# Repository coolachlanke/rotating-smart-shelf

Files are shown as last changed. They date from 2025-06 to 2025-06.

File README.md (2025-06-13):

# Rotating Smart Shelf

Motorised display shelf for Rubik’s Cubes and other collectibles, powered by ESP32-C3 and WS2812B RGB LEDs.  
Designed for showpieces, timed rotations and eye-catching animations.

---

## 🧰 Tech Stack

- **Microcontroller:** ESP32-C3 (BLE, WiFi)
- **PCBs:** Custom power distrubution/driver/logic board + annular 48-pixel WS21812B carrier board. All designed in KiCAD 8.
- **Motors:** NEMA17 bipolar stepper motors with A4988 drivers
- **Power:** 9V barrel input with onboard 5V & 3V3 voltage regulation
- **Firmware:** Custom C++ firmware utiliting FreeRTOS built with PlatformIO (Arduino framework)
- **Lighting:** WS2812B addressable RGB LED rings for reactive effects
- **Control App:** Web-app interface for wireless control and presets
- **Features:**
  - Smooth timed rotation of platforms
  - Colour animations, brightness modulation, visual syncing
  - [UNDER CONSTRUCTION] Optional music-reactive visuals (via onboard mic or wireless data stream)

---

> Designed by Lachlan Cooke in late 2024.
> Check out [lachlancooke.com/projects](https://www.lachlancooke.com/projects) für mehr details.

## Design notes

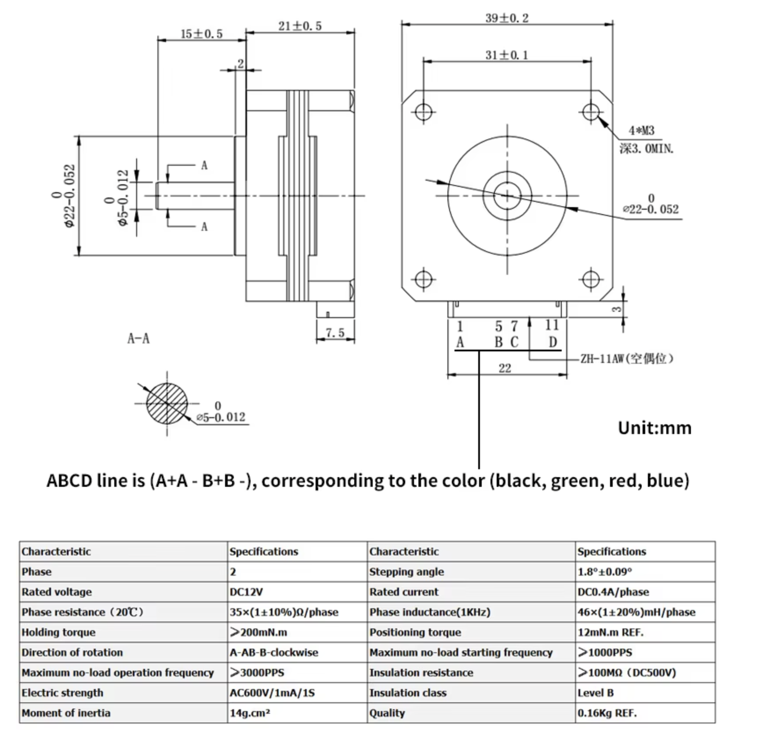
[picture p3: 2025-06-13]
Images/17HS08-1004S_Schematic.png

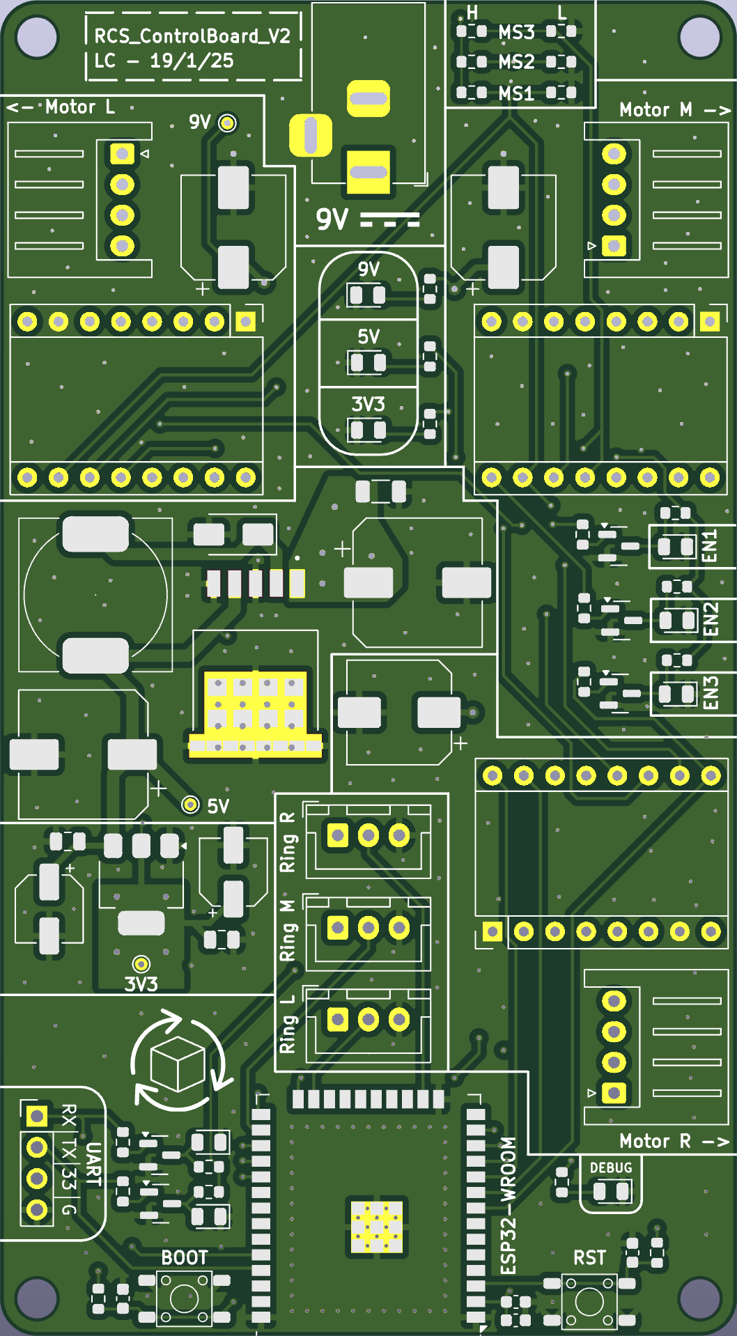
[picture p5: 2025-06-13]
CAD/Mechanical/3DP_Outjobs/RCS_Proto_V2/RCS_Logic_V2_FrontSilk.png

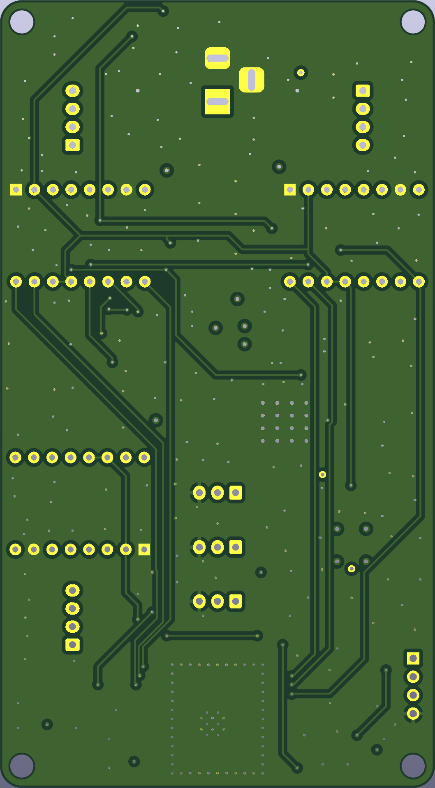
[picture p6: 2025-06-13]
CAD/Mechanical/3DP_Outjobs/RCS_Proto_V2/RCS_Logic_V2_BottomSilk.png

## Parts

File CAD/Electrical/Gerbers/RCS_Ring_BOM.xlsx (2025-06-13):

Comment | Designator | Footprint | JLCPCB Part #
100nF | C1, C2, C3, C4, C5, C6, C7, C8, C9, C10, C11, C12, C13, C14, C15, C16, C17, C18, C19, C20, C21, C22, C23, C24, C25, C26, C27, C28, C29, C30, C31, C32, C33, C34, C35, C36, C37, C38, C39, C40, C41, C42, C43, C44, C45, C46, C47, C48 | C0603 | C14663
WS2812B | D1, D2, D3, D4, D5, D6, D7, D8, D9, D10, D11, D12, D13, D14, D15, D16, D17, D18, D19, D20, D21, D22, D23, D24, D25, D26, D27, D28, D29, D30, D31, D32, D33, D34, D35, D36, D37, D38, D39, D40, D41, D42, D43, D44, D45, D46, D47, D48 | LED_WS2812B-2020_PLCC4_2.0x2.0mm | C965555

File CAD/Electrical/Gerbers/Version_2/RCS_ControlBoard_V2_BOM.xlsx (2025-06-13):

Comment | Designator | Footprint | JLCPCB Part #
100u Electrolytic | C1,C5,C9 | Capacitor_SMD:CP_Elec_8x10 | C116241
680u Electrolytic | C2 | Capacitor_SMD:CP_Elec_10x10 | C340751
1u 1206 | C3 | Capacitor_SMD:C_1206_3216Metric | C1848
220u Electrolytic | C4 | Capacitor_SMD:CP_Elec_10x10 | C125977
10u Electrolytic | C6,C8 | Capacitor_SMD:CP_Elec_5x5.4 | C4747971
10u 0603 | C14 | Capacitor_SMD:C_0603_1608Metric | C19702
0.1u 0805 | C7,C12 | Capacitor_SMD:C_0805_2012Metric | C28233
0.1u 0603 | C10,C11,C13 | Capacitor_SMD:C_0603_1608Metric | C1588
SS34 | D1 | Diode_SMD:D_SMA | C8678
LED (GRE) | D2,D3,D4 | Diode_SMD:D_0805_2012Metric | C965815
LED (RED) | D5,D8,D9 | Diode_SMD:D_0805_2012Metric | C965812
LED (BLU) | D6, D10 | Diode_SMD:D_0805_2012Metric | C965817
LED (YEL) | D7 | Diode_SMD:D_0805_2012Metric | C965814
Barrel_Jack | J1 | Connector_BarrelJack:BarrelJack_Horizontal | C136744
Conn_01x04 | J2,J3,J4 | Connector_JST:JST_XH_S4B-XH-A_1x04_P2.50mm_Horizontal | C157925
Conn_01x03 | J5,J6,J7 | Connector_JST:JST_XH_B3B-XH-A_1x03_P2.50mm_Vertical | C161870
Conn_01x04_Pin | J8 | Connector_PinHeader_2.54mm:PinHeader_1x04_P2.54mm_Vertical | C2691448
33uH | L1 | LC_CustomFootprint:SMDRI127 | C9400
BC817 | Q1,Q2,Q3,Q4,Q5 | Package_TO_SOT_SMD:SOT-23 | C52801
0R | R1,R2,R3,R19,R20,R21 | Resistor_SMD:R_0603_1608Metric | C21189
750R | R4, R22 | Resistor_SMD:R_0603_1608Metric | C23179
1k | R7,R8,R9,R10,R15,R16,R17,R18 | Resistor_SMD:R_0603_1608Metric | C21190
2k4 | R5 | Resistor_SMD:R_0603_1608Metric | C22940
6k2 | R6 | Resistor_SMD:R_0603_1608Metric | C4260
10k | R11,R12,R13,R14 | Resistor_SMD:R_0603_1608Metric | C25804
SW_Push | SW1,SW2 | LC_CustomFootprint:SW_PUSH_4.5mm | C455243
LM2596S-5 | U1 | Package_TO_SOT_SMD:TO-263-5_TabPin3 | C10002
AMS1117-3.3 | U3 | Package_TO_SOT_SMD:SOT-223-3_TabPin2 | C6186
ESP32-WROOM-32-N4 | U2 | RF_Module:ESP32-WROOM-32 | C82899

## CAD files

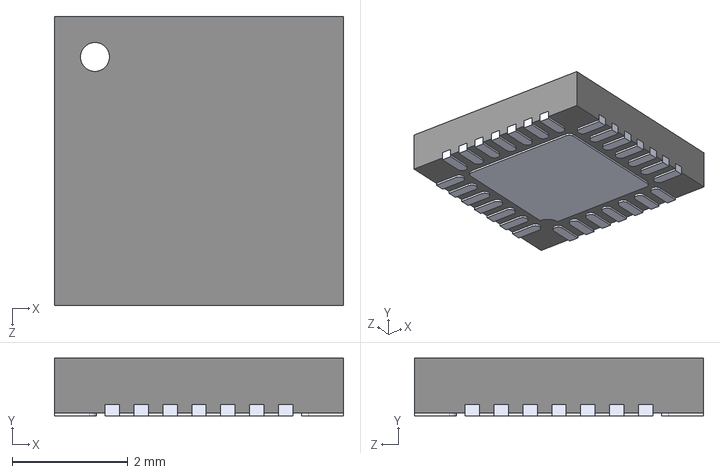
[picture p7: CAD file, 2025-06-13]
CAD/Electrical/Components/A4988SETTR_T/A4988SETTR-T.step
5.00 x 1.00 x 5.00 mm

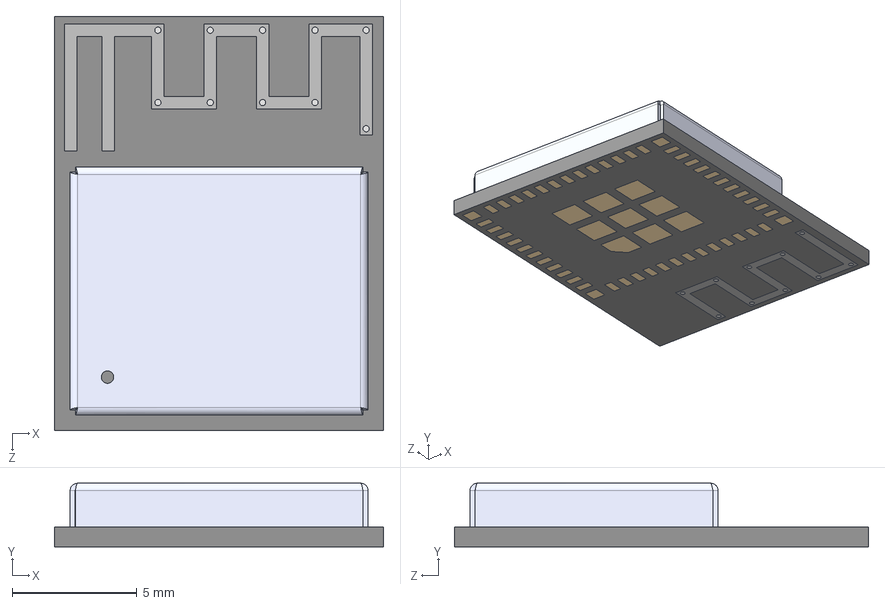
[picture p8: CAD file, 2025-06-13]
CAD/Electrical/Components/ESP32_C3_MINI_1_N4/ESP32-C3-MINI-1-N4.step
13.2 x 2.55 x 16.6 mm

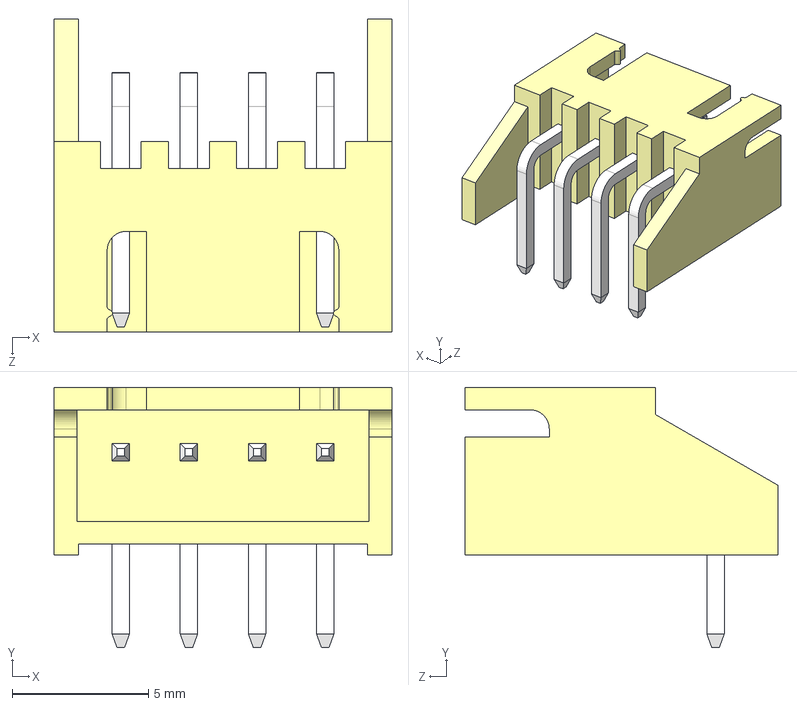
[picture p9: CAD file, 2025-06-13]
CAD/Electrical/Components/S4B-XH-A_LF__SN_/S4B-XH-A_LF__SN_.step
12.4 x 9.55 x 11.5 mm

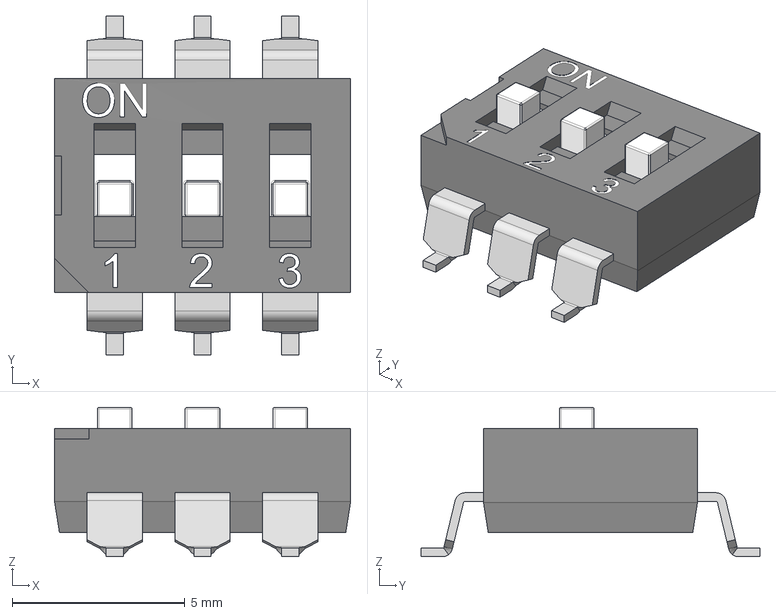
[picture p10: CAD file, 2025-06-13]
CAD/Electrical/Components/SMD DIP SWITCH 3P.step
8.56 x 9.80 x 4.32 mm

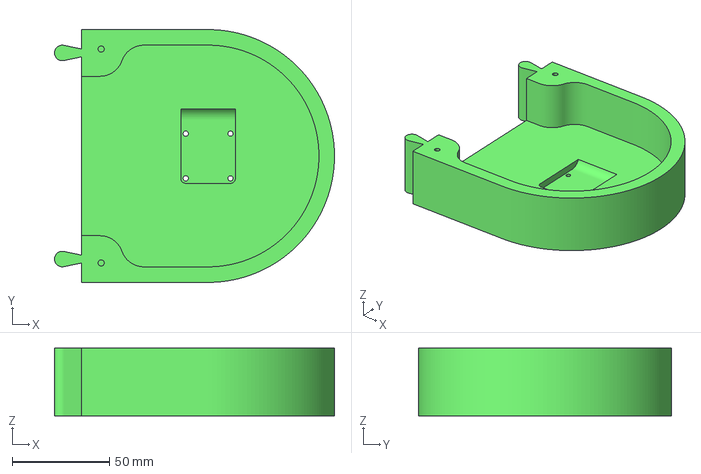
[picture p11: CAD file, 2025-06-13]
CAD/Mechanical/3DP_Outjobs/Alternate_RCS/ARCS_FrameLower_R.3mf
144.0 x 130.0 x 34.8 mm

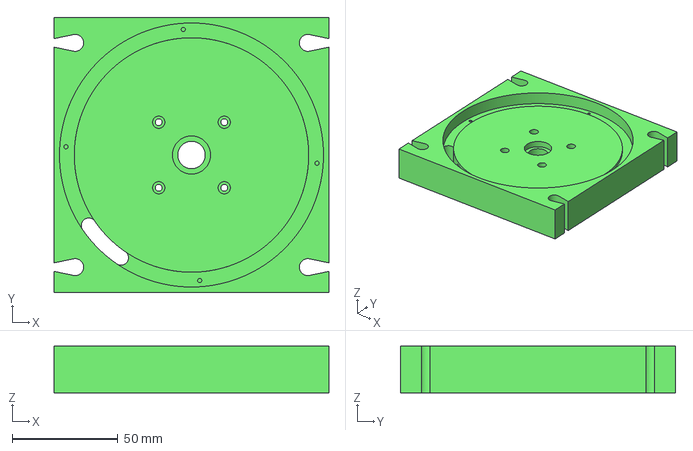
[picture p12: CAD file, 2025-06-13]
CAD/Mechanical/3DP_Outjobs/RCS_Proto_V2/Frame_M_Long.3mf
130.0 x 130.0 x 22.0 mm

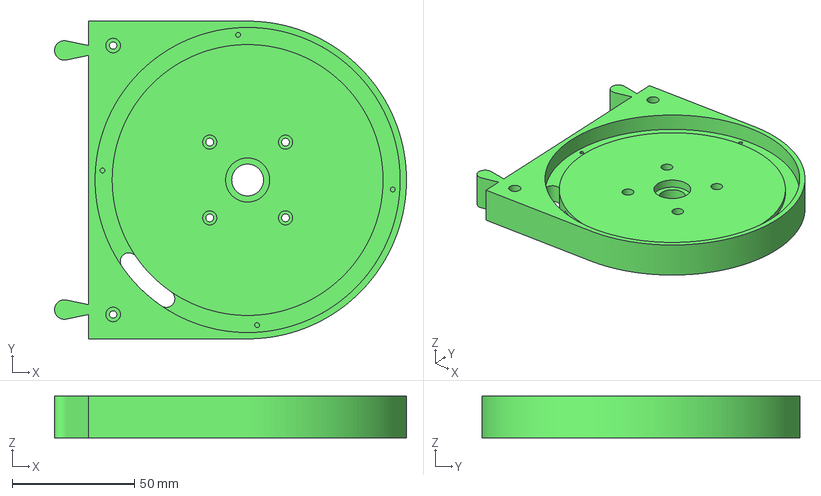
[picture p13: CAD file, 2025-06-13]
CAD/Mechanical/Current Models/2RCS_Frame_R.3mf
144.0 x 130.0 x 17.0 mm

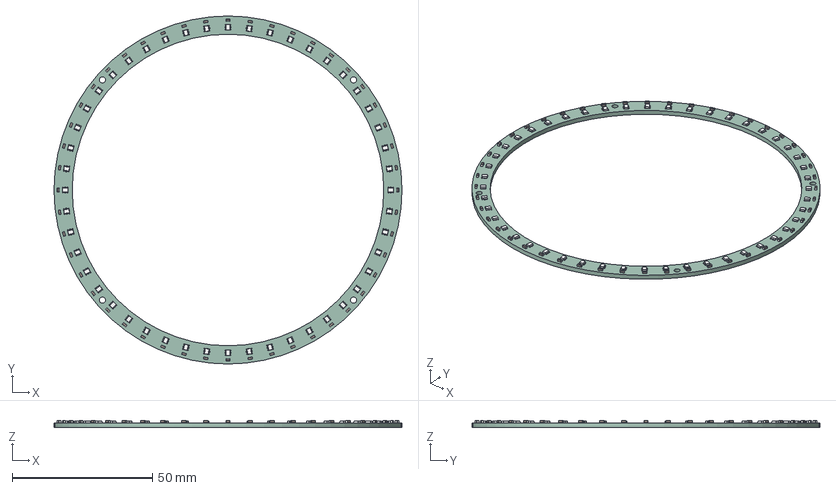
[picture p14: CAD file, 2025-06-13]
CAD/Mechanical/KiCAD_Models/RCS_WS2812B_Ring.step
124.0 x 124.0 x 2.45 mm
WS2812-2020 x 48
C_0603_1608Metric x 48
RCS_WS2812B_Ring_PCB

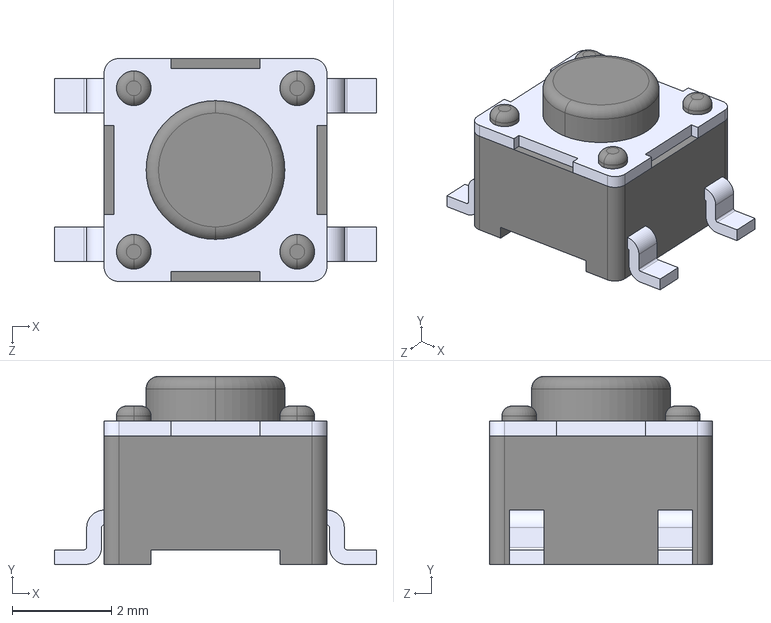
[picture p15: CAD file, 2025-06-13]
CAD/Electrical/Components/PTS 647 SM38 SMTR2 LFS--3DModel-STEP-269445.STEP
6.50 x 3.80 x 4.50 mm

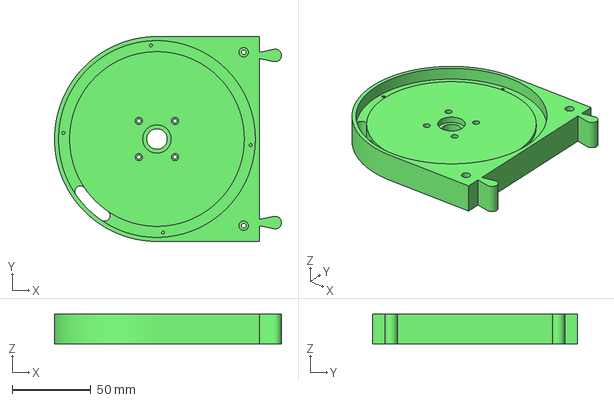
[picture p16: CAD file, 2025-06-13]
CAD/Mechanical/3DP_Outjobs/Alternate_RCS/ARCS_Frame_L2.3mf
144.0 x 130.0 x 19.0 mm

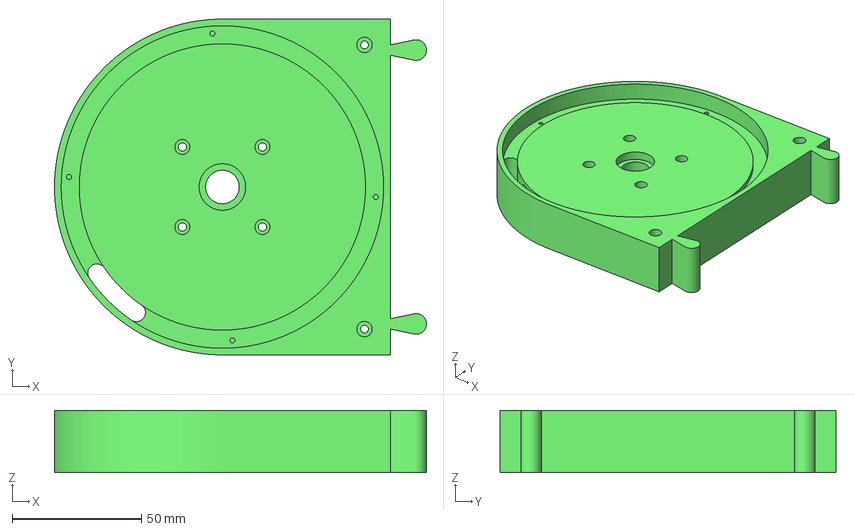
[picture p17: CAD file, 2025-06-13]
CAD/Mechanical/3DP_Outjobs/RCS_Proto_V2/Frame_L_Max.3mf
144.0 x 130.0 x 24.0 mm

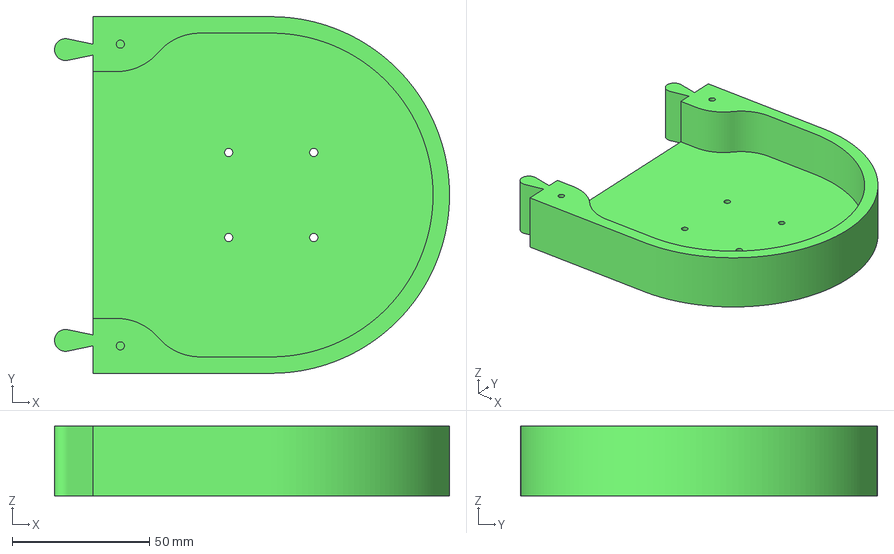
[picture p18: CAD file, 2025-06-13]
CAD/Mechanical/Current Models/2RCS_FrameLower_R.3mf
144.0 x 130.0 x 25.5 mm

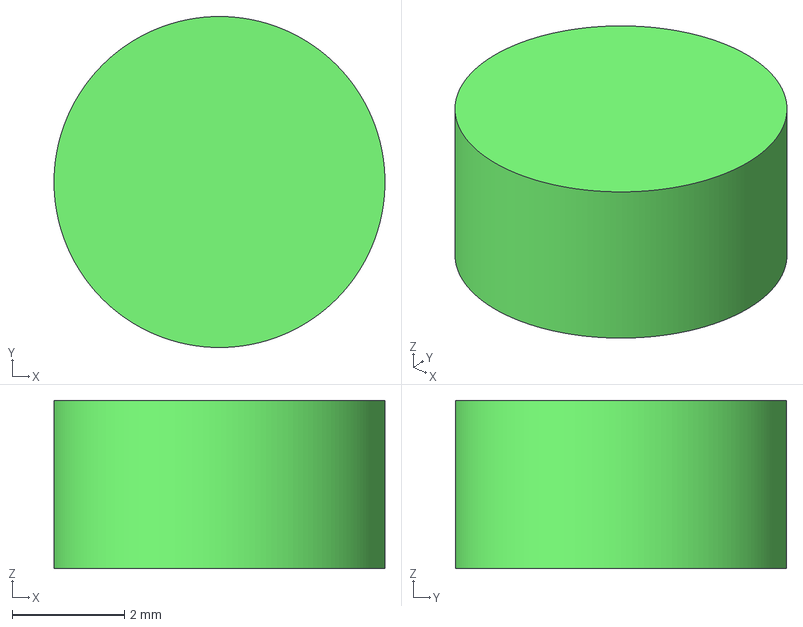
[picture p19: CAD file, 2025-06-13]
CAD/Mechanical/3DP_Outjobs/Alternate_RCS/ARCS_Cap2.3mf
5.90 x 5.90 x 3.00 mm

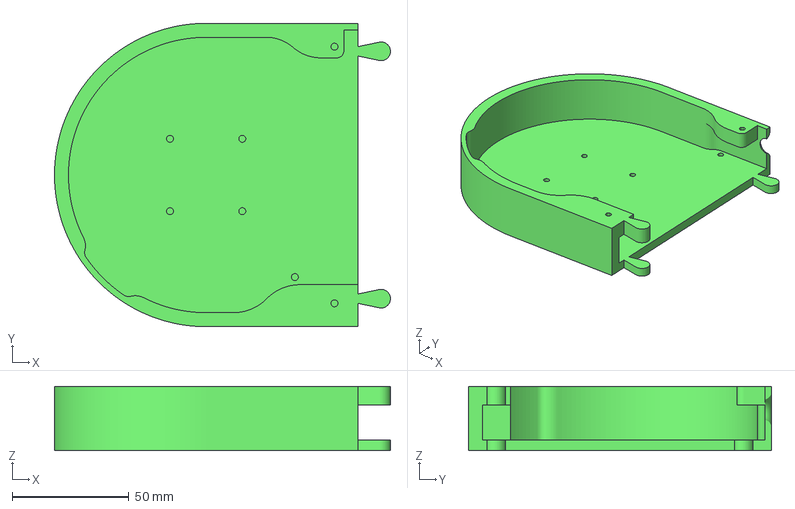
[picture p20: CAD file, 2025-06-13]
CAD/Mechanical/3DP_Outjobs/RCS_Proto_V2/FrameLower_L_MAX.3mf
144.0 x 130.0 x 27.5 mm

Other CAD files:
CAD/Mechanical/Current Models/2RCS_FrameLower_M.3mf
CAD/Electrical/Components/L_12x12mm_H8mm.step
CAD/Mechanical/3DP_Outjobs/Alternate_RCS/ARCS_Frame_L.3mf
CAD/Mechanical/3DP_Outjobs/Alternate_RCS/ARCS_Cap.3mf
CAD/Mechanical/3DP_Outjobs/Alternate_RCS/ARCS_FrameLower_L.3mf
CAD/Mechanical/3DP_Outjobs/Alternate_RCS/ARCS_FrameLower_L2.3mf
CAD/Mechanical/3DP_Outjobs/Alternate_RCS/ARCS_FrameLower_M.3mf
CAD/Mechanical/3DP_Outjobs/Alternate_RCS/ARCS_FrameLower_M_ALT.3mf
CAD/Mechanical/3DP_Outjobs/Alternate_RCS/ARCS_FrameLower_R2.3mf
CAD/Mechanical/3DP_Outjobs/Alternate_RCS/ARCS_Frame_M.3mf
CAD/Mechanical/3DP_Outjobs/Alternate_RCS/ARCS_Frame_R.3mf
CAD/Mechanical/3DP_Outjobs/Alternate_RCS/ARCS_Frame_R2.3mf
CAD/Mechanical/3DP_Outjobs/Alternate_RCS/ARCS_Platform.3mf
CAD/Mechanical/3DP_Outjobs/Alternate_RCS/ARCS_Platform2.3mf
CAD/Mechanical/3DP_Outjobs/RCS_Proto_V1/Diffuser.3mf
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

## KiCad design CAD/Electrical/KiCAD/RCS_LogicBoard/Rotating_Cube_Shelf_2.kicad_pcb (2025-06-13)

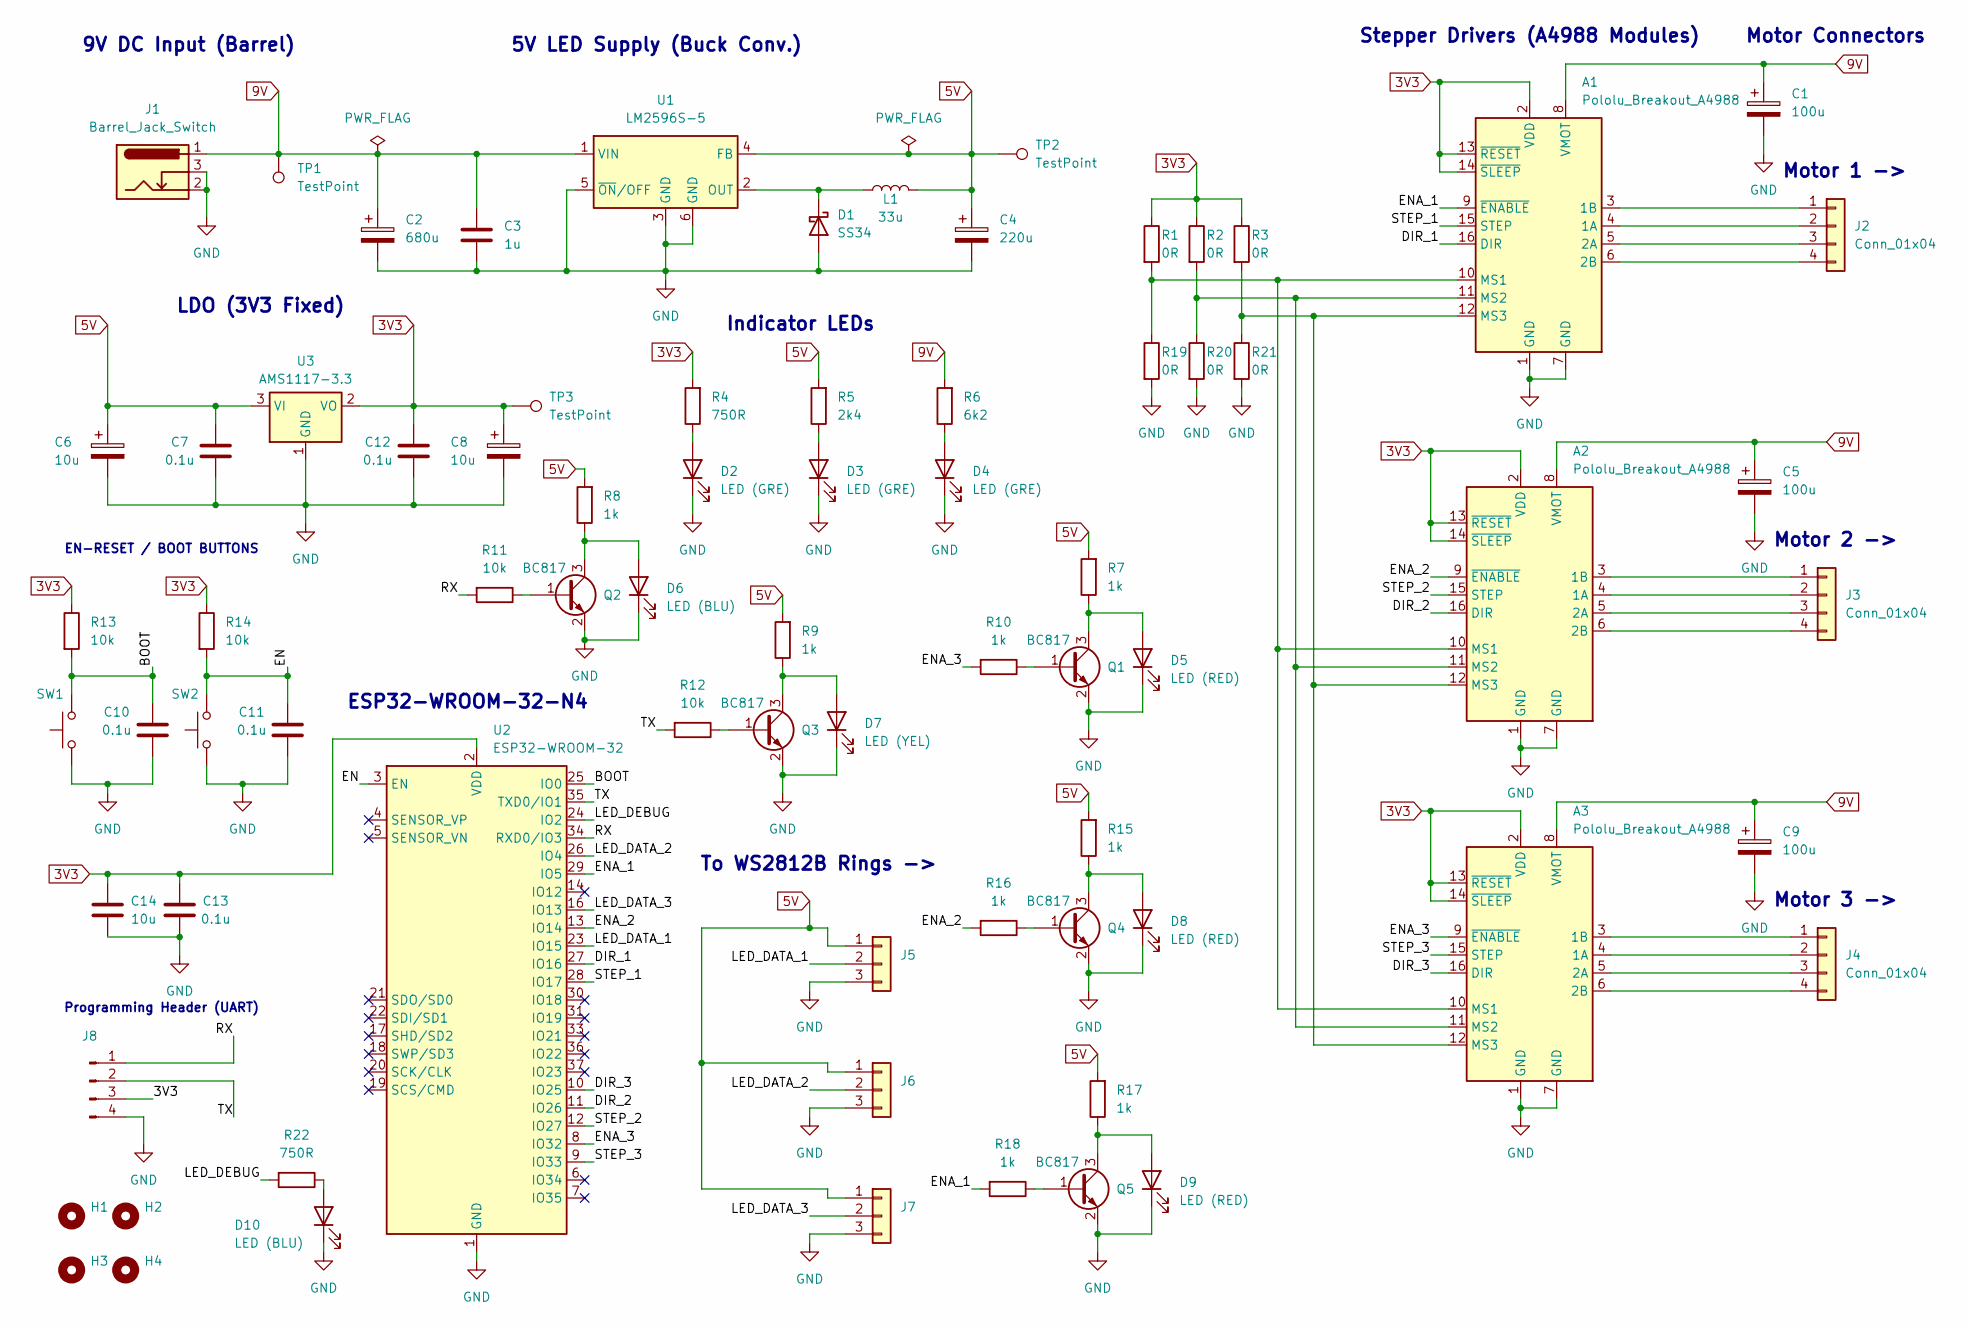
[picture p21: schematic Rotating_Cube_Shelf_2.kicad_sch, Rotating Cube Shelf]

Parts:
A1, A2, A3: Pololu_Breakout_A4988; Pololu_Breakout-16_15.2x20.3mm
C1, C5, C9: 100u; CP_Elec_8x10; LCSC C116241
C2: 680u; CP_Elec_10x10; LCSC C340751
C3: 1u; C_1206_3216Metric
C4: 220u; CP_Elec_10x10; LCSC C125977
C6, C8: 10u; CP_Elec_5x5.4; LCSC C4747971
C7, C12: 0.1u; C_0805_2012Metric
C10, C11, C13: 0.1u; C_0603_1608Metric
C14: 10u; C_0603_1608Metric
D1: SS34; D_SMA
D2, D3, D4: LED (GRE); D_0805_2012Metric; LCSC C965815
D5, D8, D9: LED (RED); D_0805_2012Metric; LCSC C965812
D6, D10: LED (BLU); D_0805_2012Metric; LCSC C965817
D7: LED (YEL); D_0805_2012Metric; LCSC C965814
H1, H2, H3, H4: MountingHole; MountingHole_3.2mm_M3
J1: Barrel_Jack_Switch; BarrelJack_Horizontal; LCSC C136744
J2, J3, J4: Conn_01x04; JST_XH_S4B-XH-A_1x04_P2.50mm_Horizontal; LCSC C157925
J5, J6, J7: Conn_01x03; JST_XH_B3B-XH-A_1x03_P2.50mm_Vertical; LCSC C161870
J8: Conn_01x04_Pin; PinHeader_1x04_P2.54mm_Vertical; LCSC C2691448
L1: 33u; SMDRI127; LCSC C9400
Q1, Q2, Q3, Q4, Q5: BC817; SOT-23; LCSC C52801
R1, R2, R3, R19, R20, R21: 0R; R_0603_1608Metric
R4, R22: 750R; R_0603_1608Metric
R5: 2k4; R_0603_1608Metric
R6: 6k2; R_0603_1608Metric
R7, R8, R9, R10, R15, R16, R17, R18: 1k; R_0603_1608Metric
R11, R12, R13, R14: 10k; R_0603_1608Metric
SW1, SW2: SW_Push; SW_PUSH_4.5mm; LCSC C455243
TP1, TP2, TP3: TestPoint; TestPoint_THTPad_D1.0mm_Drill0.5mm
U1: LM2596S-5; VREG_LM2596SX-5.0_NOPB
U2: ESP32-WROOM-32; LCSC C82899
U3: AMS1117-3.3; SOT-223-3_TabPin2; LCSC C6186

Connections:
3V3: A1.2 (VDD), A1.13 (~RESET), A1.14 (~SLEEP), A2.2 (VDD), A2.13 (~RESET), A2.14 (~SLEEP), A3.2 (VDD), A3.13 (~RESET), A3.14 (~SLEEP), C8.1, C12.2, C13.2, C14.2, J8.3, R1.1, R2.1, R3.1, R4.2, R13.1, R14.1, TP3.1, U2.2 (VDD), U3.2 (VO)
5V: C4.1, C6.1, C7.2, J5.1, J6.1, J7.1, L1.2, R5.2, R7.2, R8.2, R9.2, R15.2, R17.2, TP2.1, U1.4 (FB), U3.3 (VI)
9V: A1.8 (VMOT), A2.8 (VMOT), A3.8 (VMOT), C1.1, C2.1, C3.2, C5.1, C9.1, J1.1, R6.2, TP1.1, U1.1 (VIN)
/BOOT: C10.2, R13.2, SW1.2, U2.25 (IO0)
/DIR_1: A1.16 (DIR), U2.27 (IO16)
/DIR_2: A2.16 (DIR), U2.11 (IO26)
/DIR_3: A3.16 (DIR), U2.10 (IO25)
/EN: C11.2, R14.2, SW2.2, U2.3 (EN)
/ENA_1: A1.9 (~ENABLE), R18.2, U2.29 (IO5)
/ENA_2: A2.9 (~ENABLE), R16.2, U2.13 (IO14)
/ENA_3: A3.9 (~ENABLE), R10.2, U2.8 (IO32)
/LED_DATA_1: J5.2, U2.23 (IO15)
/LED_DATA_2: J6.2, U2.26 (IO4)
/LED_DATA_3: J7.2, U2.16 (IO13)
/LED_DEBUG: R22.2, U2.24 (IO2)
/RX: J8.1, R11.2, U2.34 (RXD0/IO3)
/STEP_1: A1.15 (STEP), U2.28 (IO17)
/STEP_2: A2.15 (STEP), U2.12 (IO27)
/STEP_3: A3.15 (STEP), U2.9 (IO33)
/TX: J8.2, R12.2, U2.35 (TXD0/IO1)
GND: A1.1 (GND), A1.7 (GND), A2.1 (GND), A2.7 (GND), A3.1 (GND), A3.7 (GND), C1.2, C2.2, C3.1, C4.2, C5.2, C6.2, C7.1, C8.2, C9.2, C10.1, C11.1, C12.1, C13.1, C14.1, D1.2 (A), D2.1 (K), D3.1 (K), D4.1 (K), D5.1 (K), D6.1 (K), D7.1 (K), D8.1 (K), D9.1 (K), D10.1 (K), J1.2, J1.3, J5.3, J6.3, J7.3, J8.4, Q1.2 (E), Q2.2 (E), Q3.2 (E), Q4.2 (E), Q5.2 (E), R19.2, R20.2, R21.2, SW1.1, SW2.1, U1.3 (GND), U1.5 (~ON/OFF), U1.6 (GND), U2.1 (GND), U2.15 (GND), U2.38 (GND), U2.39 (GND), U3.1 (GND)
unnamed: A1.4 (1A), J2.2
unnamed: A1.3 (1B), J2.1
unnamed: A1.5 (2A), J2.3
unnamed: A1.6 (2B), J2.4
unnamed: A1.10 (MS1), A2.10 (MS1), A3.10 (MS1), R1.2, R19.1
unnamed: A1.11 (MS2), A2.11 (MS2), A3.11 (MS2), R2.2, R20.1
unnamed: A1.12 (MS3), A2.12 (MS3), A3.12 (MS3), R3.2, R21.1
unnamed: A2.4 (1A), J3.2
unnamed: A2.3 (1B), J3.1
unnamed: A2.5 (2A), J3.3
unnamed: A2.6 (2B), J3.4
unnamed: A3.4 (1A), J4.2
unnamed: A3.3 (1B), J4.1
unnamed: A3.5 (2A), J4.3
unnamed: A3.6 (2B), J4.4
unnamed: D1.1 (K), L1.1, U1.2 (OUT)
unnamed: D2.2 (A), R4.1
unnamed: D3.2 (A), R5.1
unnamed: D4.2 (A), R6.1
unnamed: D5.2 (A), Q1.3 (C), R7.1
unnamed: D6.2 (A), Q2.3 (C), R8.1
unnamed: D7.2 (A), Q3.3 (C), R9.1
unnamed: D8.2 (A), Q4.3 (C), R15.1
unnamed: D9.2 (A), Q5.3 (C), R17.1
unnamed: D10.2 (A), R22.1
unnamed: Q1.1 (B), R10.1
unnamed: Q2.1 (B), R11.1
unnamed: Q3.1 (B), R12.1
unnamed: Q4.1 (B), R16.1
unnamed: Q5.1 (B), R18.1

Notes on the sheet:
Stepper Drivers (A4988 Modules)
5V LED Supply (Buck Conv.)
EN-RESET / BOOT BUTTONS
To WS2812B Rings ->
Motor 3 ->
9V DC Input (Barrel)
Motor Connectors
Programming Header (UART)
Indicator LEDs
ESP32-WROOM-32-N4
Motor 1 ->
LDO (3V3 Fixed)
Motor 2 ->

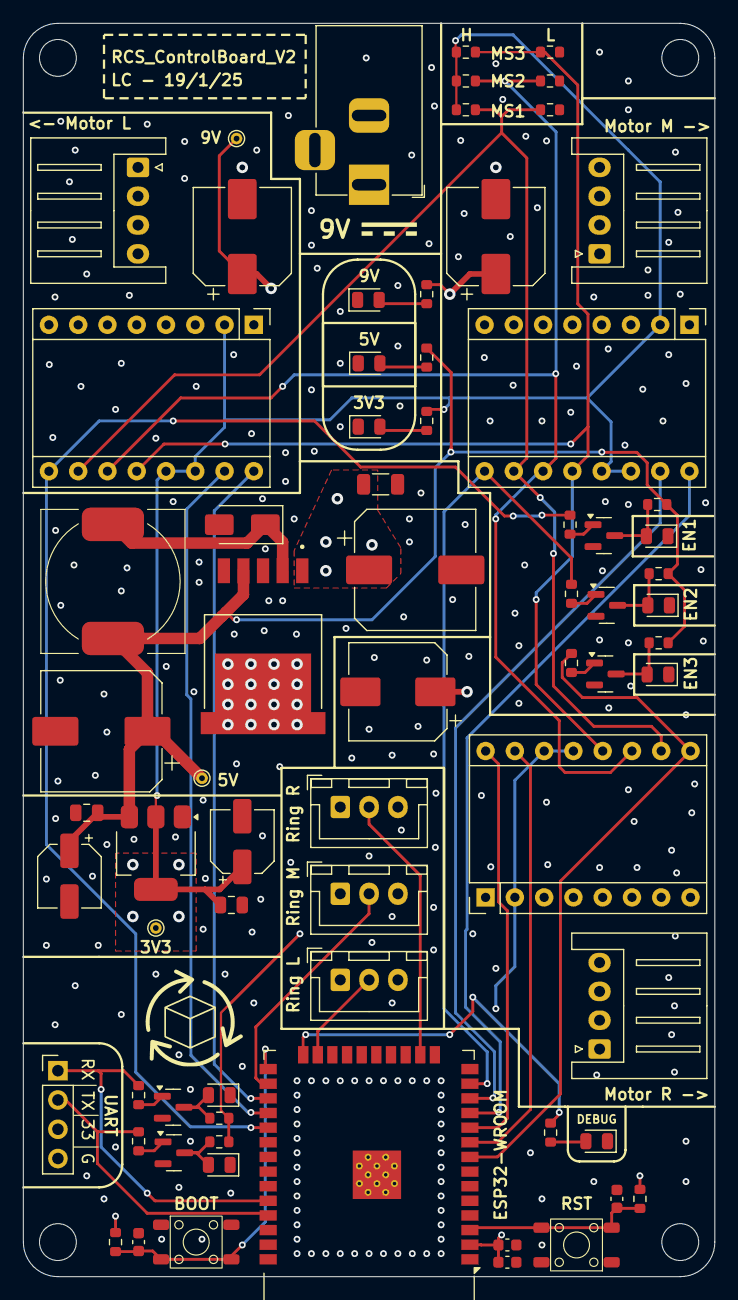
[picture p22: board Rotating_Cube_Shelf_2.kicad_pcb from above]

Board: 4 copper layers, 60.0 x 108.8 mm, 75 parts (0 on the bottom side), 51 nets.

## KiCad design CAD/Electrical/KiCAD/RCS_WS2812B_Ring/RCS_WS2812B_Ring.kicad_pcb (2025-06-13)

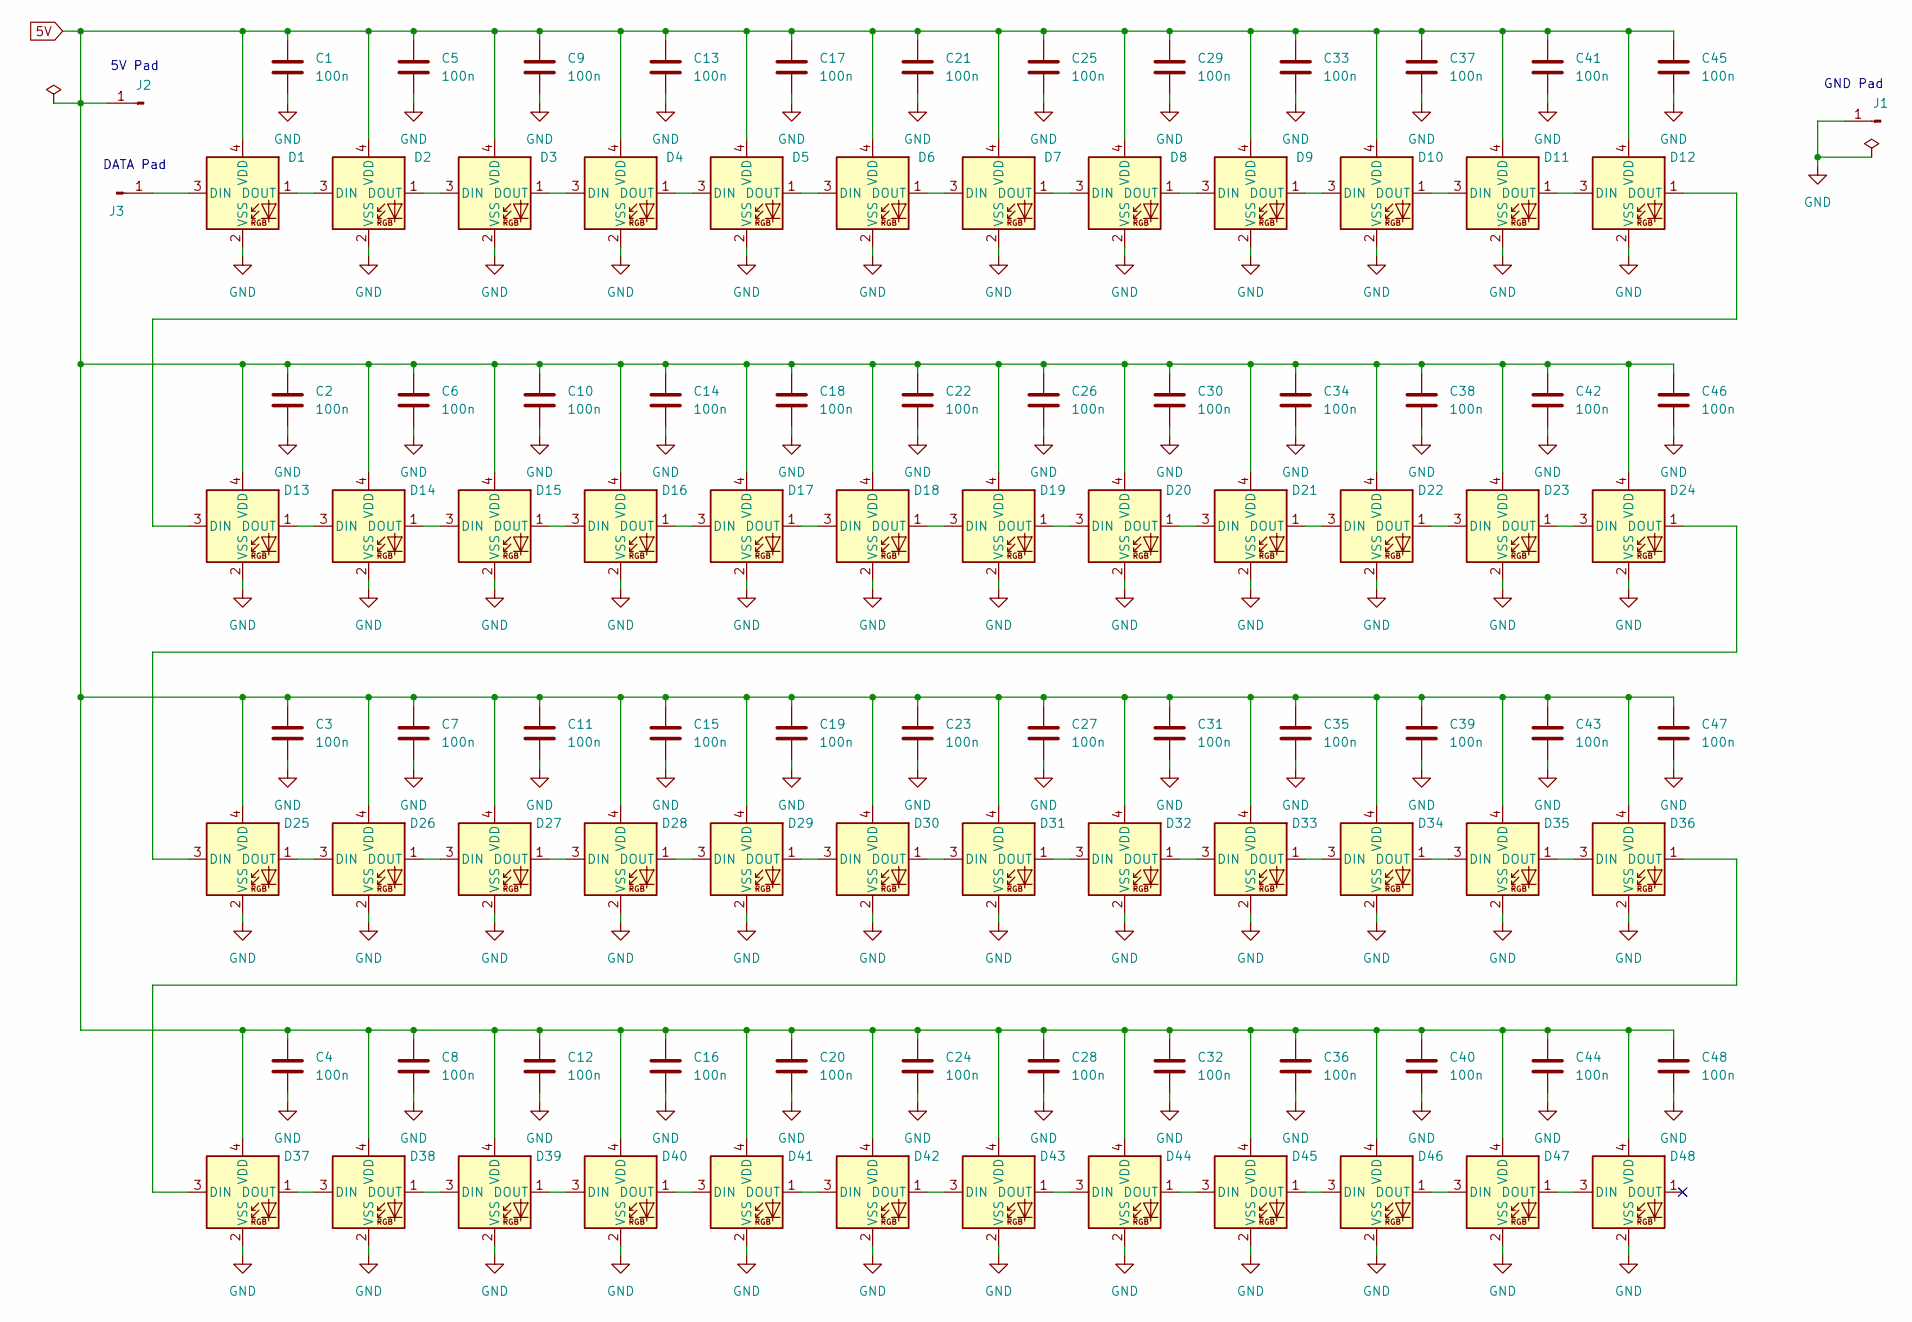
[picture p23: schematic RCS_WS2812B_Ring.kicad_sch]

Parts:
C1, C2, C3, C4, C5, C6, C7, C8, C9, C10, C11, C12, C13, C14, C15, C16, C17, C18, C19, C20, C21, C22, C23, C24, C25, C26, C27, C28, C29, C30, C31, C32, C33, C34, C35, C36, C37, C38, C39, C40, C41, C42, C43, C44, C45, C46, C47, C48: 100n; C_0603_1608Metric
D1, D2, D3, D4, D5, D6, D7, D8, D9, D10, D11, D12, D13, D14, D15, D16, D17, D18, D19, D20, D21, D22, D23, D24, D25, D26, D27, D28, D29, D30, D31, D32, D33, D34, D35, D36, D37, D38, D39, D40, D41, D42, D43, D44, D45, D46, D47, D48: WS2812B-2020; LED_WS2812B-2020_PLCC4_2.0x2.0mm
J1, J2, J3: Conn_01x01_Pin; PAD_WS2812B_RING

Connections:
5V: C1.1, C2.1, C3.1, C4.1, C5.1, C6.1, C7.1, C8.1, C9.1, C10.1, C11.1, C12.1, C13.1, C14.1, C15.1, C16.1, C17.1, C18.1, C19.1, C20.1, C21.1, C22.1, C23.1, C24.1, C25.1, C26.1, C27.1, C28.1, C29.1, C30.1, C31.1, C32.1, C33.1, C34.1, C35.1, C36.1, C37.1, C38.1, C39.1, C40.1, C41.1, C42.1, C43.1, C44.1, C45.1, C46.1, C47.1, C48.1, D1.4 (VDD), D2.4 (VDD), D3.4 (VDD), D4.4 (VDD), D5.4 (VDD), D6.4 (VDD), D7.4 (VDD), D8.4 (VDD), D9.4 (VDD), D10.4 (VDD), D11.4 (VDD), D12.4 (VDD), D13.4 (VDD), D14.4 (VDD), D15.4 (VDD), D16.4 (VDD), D17.4 (VDD), D18.4 (VDD), D19.4 (VDD), D20.4 (VDD), D21.4 (VDD), D22.4 (VDD), D23.4 (VDD), D24.4 (VDD), D25.4 (VDD), D26.4 (VDD), D27.4 (VDD), D28.4 (VDD), D29.4 (VDD), D30.4 (VDD), D31.4 (VDD), D32.4 (VDD), D33.4 (VDD), D34.4 (VDD), D35.4 (VDD), D36.4 (VDD), D37.4 (VDD), D38.4 (VDD), D39.4 (VDD), D40.4 (VDD), D41.4 (VDD), D42.4 (VDD), D43.4 (VDD), D44.4 (VDD), D45.4 (VDD), D46.4 (VDD), D47.4 (VDD), D48.4 (VDD), J2.1
GND: C1.2, C2.2, C3.2, C4.2, C5.2, C6.2, C7.2, C8.2, C9.2, C10.2, C11.2, C12.2, C13.2, C14.2, C15.2, C16.2, C17.2, C18.2, C19.2, C20.2, C21.2, C22.2, C23.2, C24.2, C25.2, C26.2, C27.2, C28.2, C29.2, C30.2, C31.2, C32.2, C33.2, C34.2, C35.2, C36.2, C37.2, C38.2, C39.2, C40.2, C41.2, C42.2, C43.2, C44.2, C45.2, C46.2, C47.2, C48.2, D1.2 (VSS), D2.2 (VSS), D3.2 (VSS), D4.2 (VSS), D5.2 (VSS), D6.2 (VSS), D7.2 (VSS), D8.2 (VSS), D9.2 (VSS), D10.2 (VSS), D11.2 (VSS), D12.2 (VSS), D13.2 (VSS), D14.2 (VSS), D15.2 (VSS), D16.2 (VSS), D17.2 (VSS), D18.2 (VSS), D19.2 (VSS), D20.2 (VSS), D21.2 (VSS), D22.2 (VSS), D23.2 (VSS), D24.2 (VSS), D25.2 (VSS), D26.2 (VSS), D27.2 (VSS), D28.2 (VSS), D29.2 (VSS), D30.2 (VSS), D31.2 (VSS), D32.2 (VSS), D33.2 (VSS), D34.2 (VSS), D35.2 (VSS), D36.2 (VSS), D37.2 (VSS), D38.2 (VSS), D39.2 (VSS), D40.2 (VSS), D41.2 (VSS), D42.2 (VSS), D43.2 (VSS), D44.2 (VSS), D45.2 (VSS), D46.2 (VSS), D47.2 (VSS), D48.2 (VSS), J1.1
unnamed: D1.3 (DIN), J3.1
unnamed: D1.1 (DOUT), D2.3 (DIN)
unnamed: D2.1 (DOUT), D3.3 (DIN)
unnamed: D3.1 (DOUT), D4.3 (DIN)
unnamed: D4.1 (DOUT), D5.3 (DIN)
unnamed: D5.1 (DOUT), D6.3 (DIN)
unnamed: D6.1 (DOUT), D7.3 (DIN)
unnamed: D7.1 (DOUT), D8.3 (DIN)
unnamed: D8.1 (DOUT), D9.3 (DIN)
unnamed: D9.1 (DOUT), D10.3 (DIN)
unnamed: D10.1 (DOUT), D11.3 (DIN)
unnamed: D11.1 (DOUT), D12.3 (DIN)
unnamed: D12.1 (DOUT), D13.3 (DIN)
unnamed: D13.1 (DOUT), D14.3 (DIN)
unnamed: D14.1 (DOUT), D15.3 (DIN)
unnamed: D15.1 (DOUT), D16.3 (DIN)
unnamed: D16.1 (DOUT), D17.3 (DIN)
unnamed: D17.1 (DOUT), D18.3 (DIN)
unnamed: D18.1 (DOUT), D19.3 (DIN)
unnamed: D19.1 (DOUT), D20.3 (DIN)
unnamed: D20.1 (DOUT), D21.3 (DIN)
unnamed: D21.1 (DOUT), D22.3 (DIN)
unnamed: D22.1 (DOUT), D23.3 (DIN)
unnamed: D23.1 (DOUT), D24.3 (DIN)
unnamed: D24.1 (DOUT), D25.3 (DIN)
unnamed: D25.1 (DOUT), D26.3 (DIN)
unnamed: D26.1 (DOUT), D27.3 (DIN)
unnamed: D27.1 (DOUT), D28.3 (DIN)
unnamed: D28.1 (DOUT), D29.3 (DIN)
unnamed: D29.1 (DOUT), D30.3 (DIN)
unnamed: D30.1 (DOUT), D31.3 (DIN)
unnamed: D31.1 (DOUT), D32.3 (DIN)
unnamed: D32.1 (DOUT), D33.3 (DIN)
unnamed: D33.1 (DOUT), D34.3 (DIN)
unnamed: D34.1 (DOUT), D35.3 (DIN)
unnamed: D35.1 (DOUT), D36.3 (DIN)
unnamed: D36.1 (DOUT), D37.3 (DIN)
unnamed: D37.1 (DOUT), D38.3 (DIN)
unnamed: D38.1 (DOUT), D39.3 (DIN)
unnamed: D39.1 (DOUT), D40.3 (DIN)
unnamed: D40.1 (DOUT), D41.3 (DIN)
unnamed: D41.1 (DOUT), D42.3 (DIN)
unnamed: D42.1 (DOUT), D43.3 (DIN)
unnamed: D43.1 (DOUT), D44.3 (DIN)
unnamed: D44.1 (DOUT), D45.3 (DIN)
unnamed: D45.1 (DOUT), D46.3 (DIN)
unnamed: D46.1 (DOUT), D47.3 (DIN)
unnamed: D47.1 (DOUT), D48.3 (DIN)

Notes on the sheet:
GND Pad
5V Pad
DATA Pad

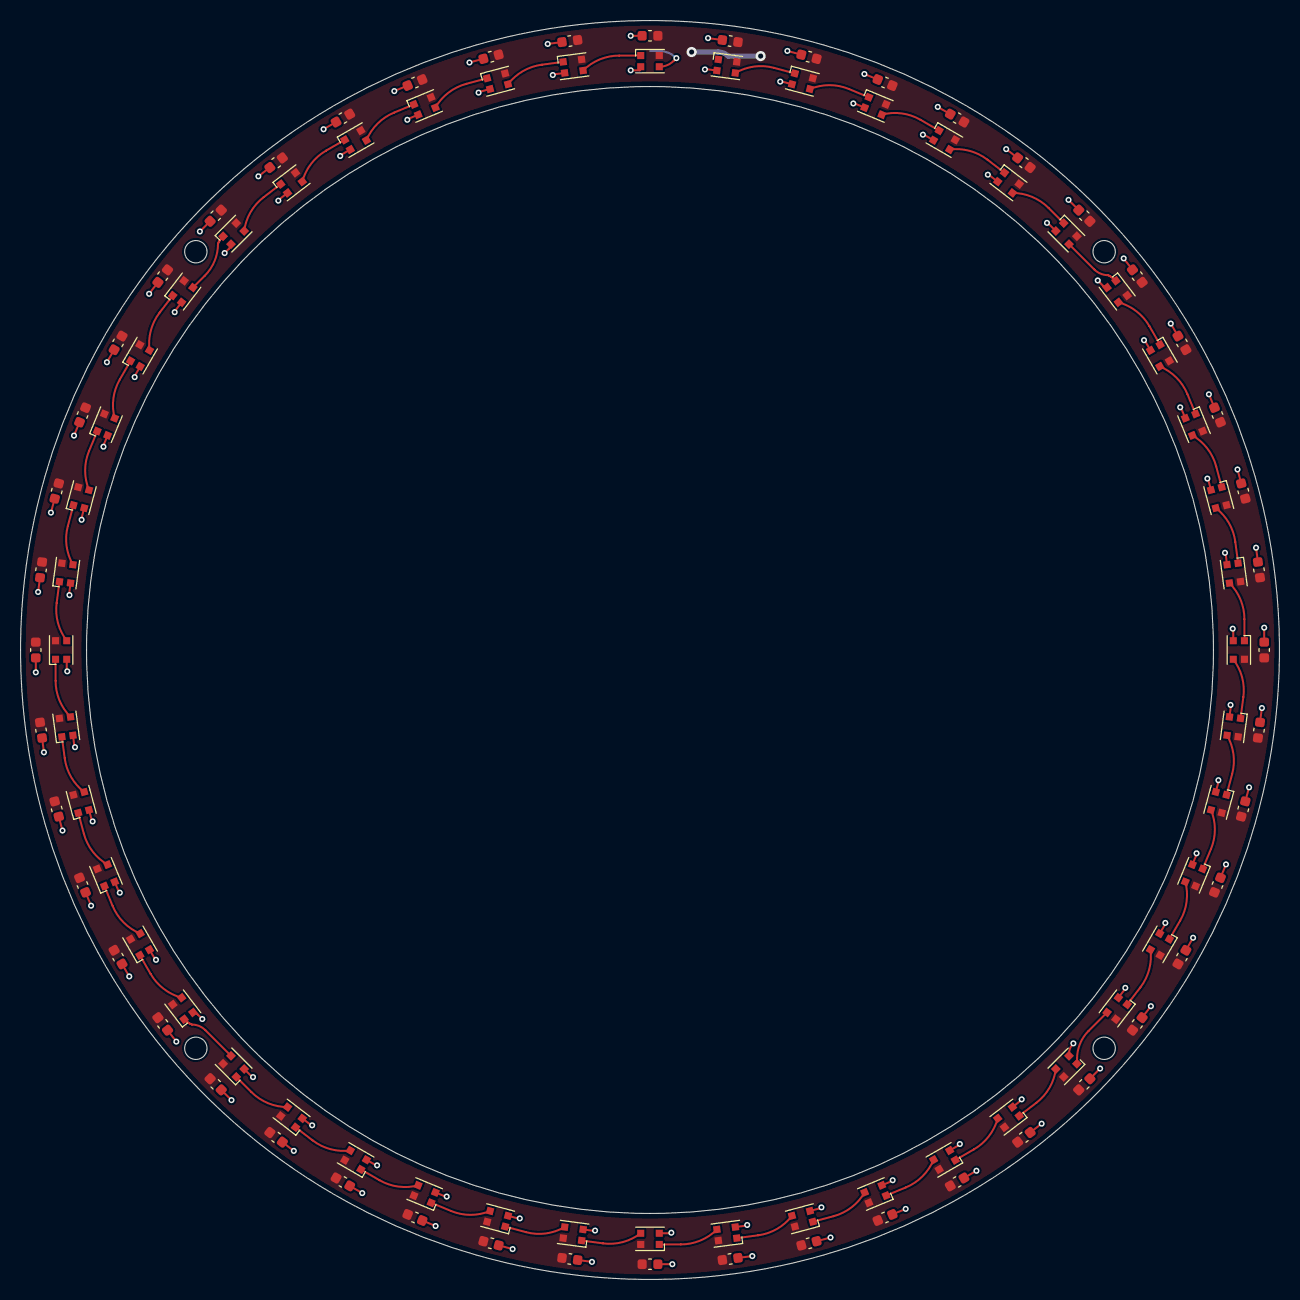
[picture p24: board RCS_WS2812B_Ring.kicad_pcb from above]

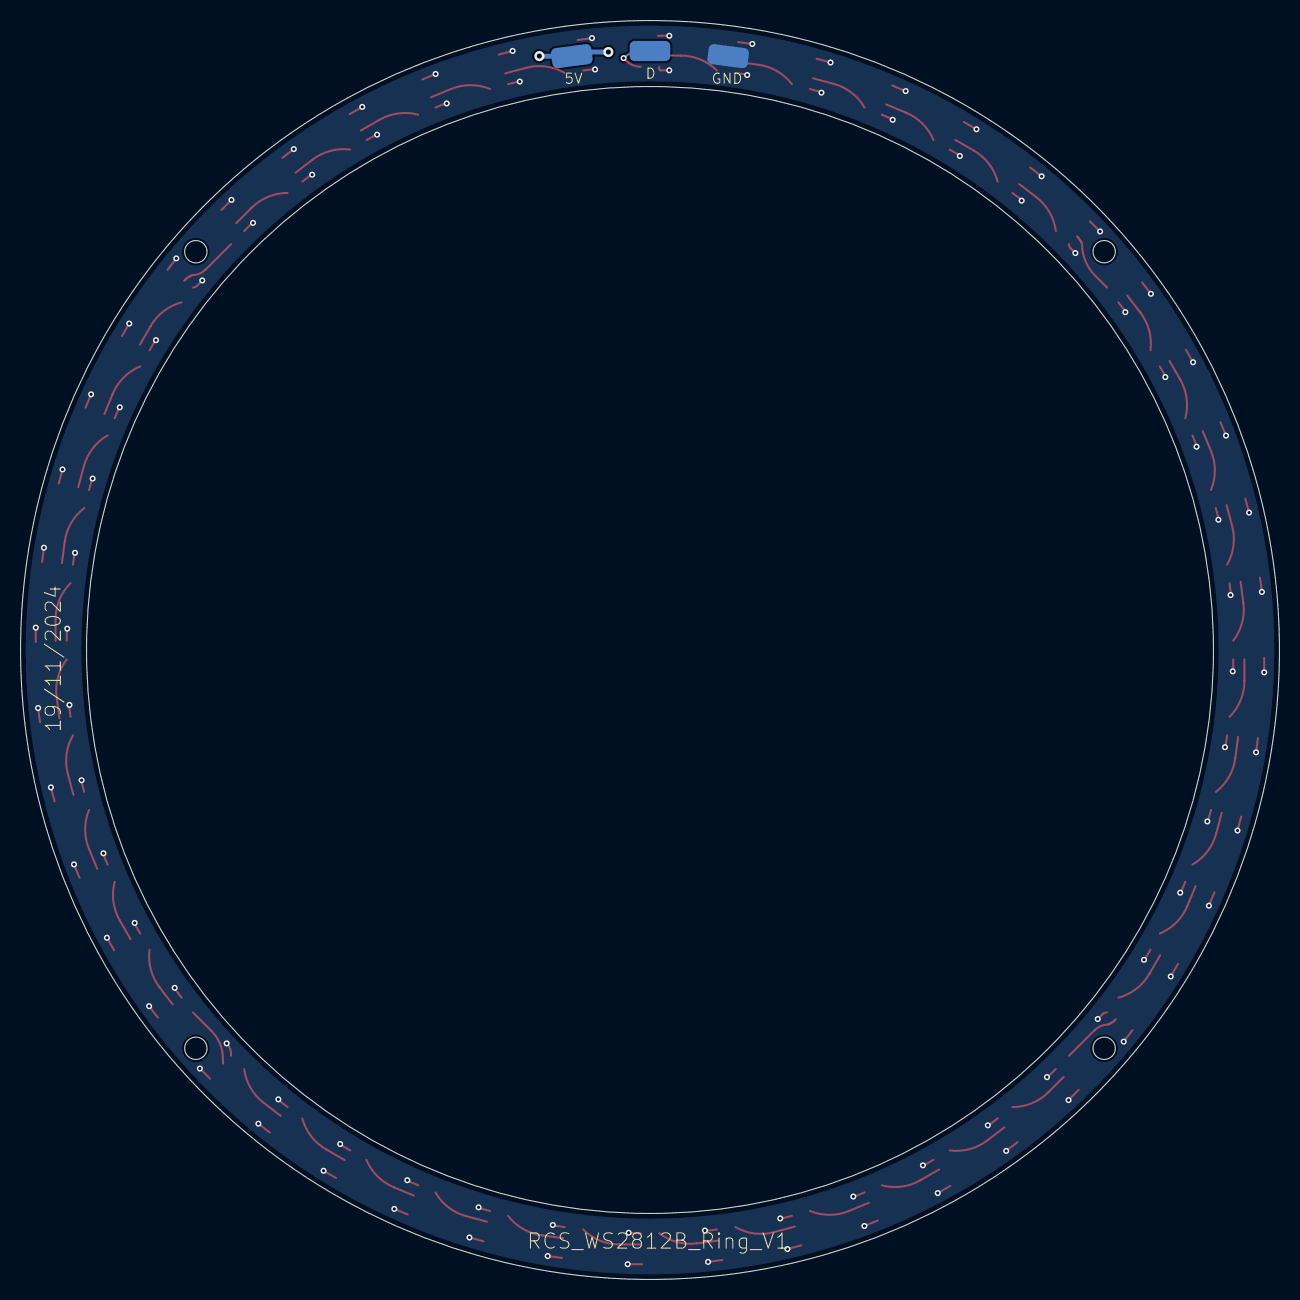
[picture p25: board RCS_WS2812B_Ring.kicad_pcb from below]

Board: 2 copper layers, 124.0 x 124.0 mm, 99 parts (3 on the bottom side), 50 nets.

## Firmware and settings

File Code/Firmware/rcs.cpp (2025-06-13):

#include <Arduino.h>
#include <AccelStepper.h>
#include <NeoPixelBus.h>
#include <WiFi.h>
A
// WS2812B LED Rings
#define LED_PIN_1 10
#define LED_PIN_2 18
#define LED_PIN_3 19
#define NUMPIXELS 48

// NeoPixelBus Objects
NeoPixelBus<NeoGrbFeature, NeoEsp32BitBangWs2812xMethod> strip1(NUMPIXELS, LED_PIN_1);
NeoPixelBus<NeoGrbFeature, NeoEsp32BitBangWs2812xMethod> strip2(NUMPIXELS, LED_PIN_2);
NeoPixelBus<NeoGrbFeature, NeoEsp32BitBangWs2812xMethod> strip3(NUMPIXELS, LED_PIN_3);

// Stepper motor control pins
#define ENA_PIN_1 9
#define STEP_PIN_1 8
#define DIR_PIN_1 7
#define ENA_PIN_2 6
#define STEP_PIN_2 5
#define DIR_PIN_2 4
#define ENA_PIN_3 1
#define STEP_PIN_3 2
#define DIR_PIN_3 3
AccelStepper stepper1(AccelStepper::DRIVER, STEP_PIN_1, DIR_PIN_1);
AccelStepper stepper2(AccelStepper::DRIVER, STEP_PIN_2, DIR_PIN_2);
AccelStepper stepper3(AccelStepper::DRIVER, STEP_PIN_3, DIR_PIN_3);

// WiFi credentials
const char* ssid = "TelstraD81AE7";
const char* password = "password";

WiFiServer server(80);

unsigned long previousMillis = 0;
const long interval = 50;  // Interval for LED update (in milliseconds)
int currentMode1 = 1;
int currentMode2 = 1;
int currentMode3 = 1;
int currentLedMode1 = 0;
int currentLedMode2 = 0;
int currentLedMode3 = 0;
unsigned long startTime1;
unsigned long startTime2;
unsigned long startTime3;
const float pi = 3.14159;   // Ya know, the circle thing
const float frequency = 0.05;     // Frequency of the sinusoidal motion (Hz)
const int microsteppingFactor = 16; // Microstepping factor

TaskHandle_t ledTaskHandle = NULL;
TaskHandle_t wifiTaskHandle = NULL;


void setup() {
  // Set up serial monitor
  Serial.begin(115200);

  // Initialize NeoPixel LED strips
  strip1.Begin();
  strip1.Show();
  strip2.Begin();
  strip2.Show();
  strip3.Begin();
  strip3.Show();
  Serial.println("NeoPixelBus initialized.");

  // Configure stepper motors
  stepper1.setMaxSpeed(1000 * microsteppingFactor);
  stepper1.setSpeed(500 * microsteppingFactor); // Set the continuous speed with microstepping factor
  stepper2.setMaxSpeed(1000 * microsteppingFactor);
  stepper2.setSpeed(500 * microsteppingFactor); // Set the continuous speed with microstepping factor
  stepper3.setMaxSpeed(1000 * microsteppingFactor);
  stepper3.setSpeed(500 * microsteppingFactor); // Set the continuous speed with microstepping factor

  // Configure WiFi
  WiFi.begin(ssid, password);
  while (WiFi.status() != WL_CONNECTED) {
    delay(500);
    Serial.print(".");
  }
  Serial.println("\nWiFi connected");
  Serial.print("IP address: ");
  Serial.println(WiFi.localIP());

  server.begin();
  startTime1 = millis();
  startTime2 = millis();
  startTime3 = millis();

  // Create LED update task
  xTaskCreatePinnedToCore(
    ledTask,          // Function to implement the task
    "LED Task",      // Name of the task
    10000,            // Stack size in words
    NULL,             // Task input parameter
    1,                // Priority of the task
    &ledTaskHandle,   // Task handle
    0                 // Core where the task should run
  );

  // Create WiFi task
  xTaskCreatePinnedToCore(
    wifiTask,         // Function to implement the task
    "WiFi Task",     // Name of the task
    10000,            // Stack size in words
    NULL,             // Task input parameter
    1,                // Priority of the task
    &wifiTaskHandle,  // Task handle
    1                 // Core where the task should run
  );
}

void loop() {
  // Run the motors based on the current mode
  runMotor(stepper1, currentMode1, startTime1, 1.0);
  runMotor(stepper2, currentMode2, startTime2, 2.0);
  runMotor(stepper3, currentMode3, startTime3, 3.0);
}

void runMotor(AccelStepper &stepper, int mode, unsigned long &startTime, float motor) {
  if (mode == 1) { // Sinusoidal motion
    unsigned long elapsedTime = millis() - startTime;
    float speed = 50 * microsteppingFactor * sin(2 * pi * frequency * (elapsedTime / 1000.0) + (2 * pi / 3) * motor);
    stepper.setSpeed(speed);
    stepper.runSpeed();
  } else if (mode == 2) { // Continuous motion
    stepper.runSpeed();
  } else if (mode == 0) { // Stop the motor
    stepper.stop();
  }
}

void ledTask(void * parameter) {
  unsigned long previousMillis = 0;
  const long interval = 50;  // Interval for LED update (in milliseconds)
  int colorWheelPos1 = 0;
  int colorWheelPos2 = 0;
  int colorWheelPos3 = 0;
  bool flashState1 = false;
  bool flashState2 = false;
  bool flashState3 = false;

  for (;;) {
    unsigned long currentMillis = millis();
    if (currentMillis - previousMillis >= interval) {
      previousMillis = currentMillis;

      // Update LED Ring 1
      updateLedRing(strip1, currentLedMode1, colorWheelPos1, flashState1);

      // Update LED Ring 2
      updateLedRing(strip2, currentLedMode2, colorWheelPos2, flashState2);

      // Update LED Ring 3
      updateLedRing(strip3, currentLedMode3, colorWheelPos3, flashState3);
    }
    vTaskDelay(10 / portTICK_PERIOD_MS); // Yield to other tasks
  }
}

// void updateLedRing(Adafruit_NeoPixel &strip, int mode, int &colorWheelPos, bool &flashState) {
void updateLedRing(NeoPixelBus<NeoGrbFeature, NeoEsp32BitBangWs2812xMethod> &strip, int mode, int &colorWheelPos) {
  switch (mode) {
    case 0: // Rainbow Effect
      for (int i = 0; i < NUMPIXELS; i++) {
        strip.SetPixelColor(i, Wheel((colorWheelPos + (i * 256 / NUMPIXELS)) & 255));
      }
      strip.show();
      colorWheelPos = (colorWheelPos + 1) % 256;
      break;

    case 1: // Solid Color (Blue)
      strip.fill(strip.Color(0, 0, 255));
      strip.show();
      break;

    case 2: // Flashing (Red)
      flashState = !flashState;
      if (flashState) {
        strip.fill(strip.Color(255, 0, 0));
      } else {
        strip.fill(strip.Color(0, 0, 0));
      }
      strip.show();
      break;

    case 3: // Theater Chase Effect (White)
      for (int i = 0; i < NUMPIXELS; i++) {
        if ((i + colorWheelPos) % 3 == 0) {
          strip.setPixelColor(i, strip.Color(255, 255, 255));
        } else {
          strip.setPixelColor(i, strip.Color(0, 0, 0));
        }
      }
      strip.show();
      colorWheelPos = (colorWheelPos + 1) % 3;
      break;
    
    case 4: // Double Sinusoidal Brightness with Color Lerp Rotation
      {
        uint32_t color = Wheel(colorWheelPos & 255); // Color based on the wheel position
        float phaseOffset = (2 * pi * colorWheelPos) / 256.0; // Smooth phase offset to avoid jumps
        for (int i = 0; i < NUMPIXELS; i++) {
          float brightness = (sin((4 * pi * i / NUMPIXELS) + phaseOffset) + 1) / 2; // Double sinusoidal brightness from 0 to 1
          uint8_t r = (uint8_t)(((color >> 16) & 0xFF) * brightness);
          uint8_t g = (uint8_t)(((color >> 8) & 0xFF) * brightness);
          uint8_t b = (uint8_t)((color & 0xFF) * brightness);
          strip.setPixelColor(i, strip.Color(r, g, b));
        }
        strip.show();
        colorWheelPos = (colorWheelPos + 3) % 256; // Increase speed of color rotation
      }

    case 5: // Perceptually Adjusted Sinusoidal Distribution
      {
          static float time = 0; // Time variable for controlling the effect
          const float speed = 0.02; // Speed of the effect
          const float maxPhase = 6 * pi; // Total phase for the pattern (multiple revolutions)

          // Custom easing function for wind-up and wind-down
          float normalizedTime = fmod(time, 1.0); // Normalize time to range [0, 1]
          float easingFactor = pow(sin(normalizedTime * pi), 2); // Smooth transition with sine

          // Calculate current phase with easing
          float phase = easingFactor * maxPhase;

          time += speed;

          uint32_t color = Wheel(colorWheelPos & 255); // Color based on wheel position
          for (int i = 0; i < NUMPIXELS; i++) {
              // Adjust sinusoidal brightness with gamma correction
              float rawBrightness = (sin((4 * pi * i / NUMPIXELS) + phase) + 1) / 2; // Original brightness
              float gammaCorrectedBrightness = pow(rawBrightness, 2.2); // Apply gamma correction (2.2 typical)

              // Map the corrected brightness to RGB values
              uint8_t r = (uint8_t)(((color >> 16) & 0xFF) * gammaCorrectedBrightness);
              uint8_t g = (uint8_t)(((color >> 8) & 0xFF) * gammaCorrectedBrightness);
              uint8_t b = (uint8_t)((color & 0xFF) * gammaCorrectedBrightness);

              // Set the pixel color
              strip.setPixelColor(i, strip.Color(r, g, b));
          }
          strip.show();

          // Update colorWheelPos to control rotation speed
          colorWheelPos = (colorWheelPos + 3) % 256;
      }

    break;
  }
}

void wifiTask(void *parameter) {
    for (;;) {
        WiFiClient client = server.available();
        if (client) {
            String request = client.readStringUntil('\r');
            //Serial.println("Client connected");
            //Serial.println("Request: " + request);
            // Serial.println(request);

            client.flush();

            // Add CORS headers to allow cross-origin requests
            client.println("HTTP/1.1 200 OK");
            client.println("Access-Control-Allow-Origin: *"); // Allow all origins
            client.println("Access-Control-Allow-Methods: GET, POST, OPTIONS"); // Allowed methods
            client.println("Access-Control-Allow-Headers: Content-Type"); // Allowed headers
            client.println("Content-type:text/plain");
            client.println();

            // Process the request
            handleRequest(request, client);

            // Close the connection
            client.stop();
            //Serial.println("Client disconnected");
        }
        vTaskDelay(10 / portTICK_PERIOD_MS); // Yield to other tasks
    }
}

void handleRequest(String request, WiFiClient &client) {
    // Trim whitespace and extract only the actual command portion
    request.trim();
    int startIndex = request.indexOf(' ') + 1; // Find the first space and move one character forward
    int endIndex = request.indexOf(' ', startIndex); // Find the next space after the command
    if (startIndex < 0 || endIndex < 0) {
        client.println("Invalid request format");
        return;
    }

    String command = request.substring(startIndex, endIndex); // Extract the command part
    Serial.println("Extracted Command:");
    Serial.println(command); // For debugging

    // Parse command format: "led_1_flashing" or "motor_2_stop"
    int firstUnderscore = command.indexOf('_');
    int secondUnderscore = command.indexOf('_', firstUnderscore + 1);

    if (firstUnderscore != -1 && secondUnderscore != -1) {
        String type = command.substring(0, firstUnderscore); // Extract "led" or "motor"
        type.remove(0, 1); // Remove leading slash
        String platform = command.substring(firstUnderscore + 1, secondUnderscore); // Extract platform code
        String mode = command.substring(secondUnderscore + 1); // Extract mode (e.g., "flashing")

        Serial.println(type);     // Debugging: Print parsed type
        Serial.println(platform); // Debugging: Print parsed platform
        Serial.println(mode);     // Debugging: Print parsed mode

        if (type == "led") {
            handleLedCommand(platform.toInt(), mode, client);
        } else if (type == "motor") {
            handleMotorCommand(platform.toInt(), mode, client);
        } else {
            client.println("Invalid type");
        }
    } else {
        client.println("Invalid command format");
    }
}


void handleLedCommand(int platform, String mode, WiFiClient &client) {
    int *currentMode = nullptr;

    // Map platform to the correct LED mode variable
    switch (platform) {
        case 1:
            currentMode = &currentLedMode1;
            break;
        case 2:
            currentMode = &currentLedMode2;
            break;
        case 3:
            currentMode = &currentLedMode3;
            break;
        default:
            client.println("Invalid LED platform");
            return;
    }

    // Map mode string to LED mode values
    if (mode == "rainbow") {
        *currentMode = 0;
        client.println("LED set to rainbow mode");
    } else if (mode == "solid") {
        *currentMode = 1;
        client.println("LED set to solid mode");
    } else if (mode == "flashing") {
        *currentMode = 2;
        client.println("LED set to flashing mode");
    } else if (mode == "theater_chase") {
        *currentMode = 3;
        client.println("LED set to theater chase mode");
    } else if (mode == "sindist") {
        *currentMode = 4;
        client.println("LED set to sinusoidal distribution mode");
    } else if (mode == "windupdown") {
        *currentMode = 5;
        client.println("LED set to wind up/down mode");
    } else {
        client.println("Invalid LED mode");
    }
}

void handleMotorCommand(int platform, String mode, WiFiClient &client) {
    int *currentMode = nullptr;

    // Map platform to the correct motor mode variable
    switch (platform) {
        case 1:
            currentMode = &currentMode1;
            break;
        case 2:
            currentMode = &currentMode2;
            break;
        case 3:
            currentMode = &currentMode3;
            break;
        default:
            client.println("Invalid motor platform");
            return;
    }

    // Map mode string to motor mode values
    if (mode == "stop") {
        *currentMode = 0;
        client.println("Motor stopped");
    } else if (mode == "sinusoidal") {
        *currentMode = 1;
        client.println("Motor set to sinusoidal mode");
    } else if (mode == "continuous") {
        *currentMode = 2;
        client.println("Motor set to continuous mode");
    } else {
        client.println("Invalid motor mode");
    }
}


uint32_t Wheel(byte WheelPos) {
  WheelPos = 255 - WheelPos;
  if (WheelPos < 85) {
    return strip1.Color(255 - WheelPos * 3, 0, WheelPos * 3);
  }
  if (WheelPos < 170) {
    WheelPos -= 85;
    return strip1.Color(0, WheelPos * 3, 255 - WheelPos * 3);
  }
  WheelPos -= 170;
  return strip1.Color(WheelPos * 3, 255 - WheelPos * 3, 0);
}
